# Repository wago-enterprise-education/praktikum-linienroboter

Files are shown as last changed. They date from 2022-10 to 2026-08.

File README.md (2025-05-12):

# Praktikum "Linien Roboter"

Dauer: ~2 Wochen  
Bachelor Projekt von Lisa Lueder  
Anpassungen durch Christian Dück und Finn Erik Hilgers  

## Inhalt

Das Repository beinhaltet das Praktikum "Linienroboter", das für Praktikanten jeden Wissensstandes für ca. 2 Wochen ausgelegt ist.

Die Ordnerstruktur wurde geändert, um die Ressourcen und die Praktikumsaufgaben logisch zu sortieren und das Praktikum übersichtlicher zu unterteilen.
Durch die neue Aufteilung ist es besser möglich, das Praktikum auch für eventuell unterschiedliche Zeiträume aufzuteilen.

### Einführung
- Kennenlernen des ESPs
- Erste Programmierübungen
- Arbeit mit den Sensoren
- Pinout und CheatSheet für den ESP und die Arduino IDE

### Löten
- Lötanleitung
- Aufgaben zum Löten des Linienroboters

### Programmieraufgaben
- Linienverfolgung
- Lichtverfolgung
- Hindernisserkennung
- Überholmanöver
- Webanwendung (Anleitung und allgemeine Idee wurde nie beendet, müsste ausgearbeitet werden)

### Ressourcen - Dateien für die Entwicklung bzw. weiterführende Aufgabenentwicklung
- 3D-Dateien für Felgen und Karosserie
- Platinenpläne
- Grundlegende Praktikums-Ideen
- Materialliste

## Ansprechpartner
- [André Bell](mailto:Andre.Bell@wago.com)
- [Tobias Lauxtermann](mailto:Tobias.Lauxtermann@wago.com)
- [Maik Rehburg](mailto:Maik.Rehburg@wago.com)

## Mitwirkende
- Lisa Rüter
- Christian Dück
- Finn Erik Hilgers
- Michael Kolle
- Louis Krumme
- Kieran Smith

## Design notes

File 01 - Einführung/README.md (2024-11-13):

# Praktikum "Linien Roboter" - Einführung

Version: V1.1  
Dauer: ~2 Wochen  
Bachelor Projekt von Lisa Lueder  
Anpassungen durch Christian Dück und Finn Erik Hilgers  

## Content

Bekanntmachen mit:
- Arduino IDE
- Elektrotechnische Grundlagen
- Informatische Grundlagen

01 -> Einführung in ESP
    Elektrotechnik + Programmiereinführung
        
Programmiereinführung anhand der elektrischen Bauteile, die auch später auf dem Roboter benutzt werden, also Beispiele an der LED, Potentiometer (Als Alternative zu den Photowiderständen) etc.

    Enthalten sind:
    - digitalWrite, digitalRead -> Hinweis zu Liniensensoren
    - pinMode
    - define
    - delay
    - Boolean -> erklärung von High und Low
    - Variablen
    - If-Bedingung
    - analogWrite, analogRead -> Hinweis zu Motoren
    - map

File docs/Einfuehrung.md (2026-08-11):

---
layout: page
title: Linienroboter - Einführung
lang: de
lang-ref: index
---

## Einführung

In der Einführung sollst du dich zunächst mit der Arduino IDE und dem ESP 32 vertraut machen sowie elektro- und informationstechnische Grundlagen erlernen, um später den Linienroboter problemlos aufbauen zu können.
Zuerst solltest du mithilfe der [Materialliste](Material.pdf) alle nötigen Bauteile zusammensuchen. Die Bauteile für diese Einleitung sind nicht in dem Bauteilsatz für den Linienroboter enthalten. Bei der Durchführung der Einführung können dir [dieses Diagramm von den Pins des ESP32](00-Pinout-ESP32-DEVKIT-V1.pdf) und [dieser Arduino Cheat Sheet](00-CheatSheet-Arduino.pdf) helfen.

{: .info}
Diese und die kommenden Anleitungen sollen dich bei deinem Praktikum unterstützen. Falls es zwischendurch Fragen geben sollte oder du anhand der Anleitung nicht weiterkommst, kannst du uns jederzeit [ansprechen](./index.md/#ansprechpartner)!

### Grundsätzliches
Wir beginnen mit dem Mikrocontroller, der den Roboter am Ende steuern wird. Das ist ein ESP32-Entwicklungsboard.

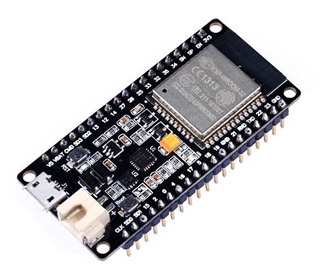
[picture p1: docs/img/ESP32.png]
Abbildung eines ESP32 DEV Board


Der eigentliche Mikrocontroller ist das silberne Quadrat in der oberen Hälfte. Der Rest sind bspw. eine WLAN-Antenne und die Stromversorgung des Mikrocontroller. Solche Mikrocontroller können z.B. für die Auswertung von Sensordaten, die Datenaufnahme oder kleinere Berechnungen eingesetzt werden.
Die Metallstifte an der Seite sind die Anschlüsse für verschiedene Schnittstellen, die der Mikrocontroller unterstützt. Wir nennen sie „Pins“. Welcher Metallstift welche Schnittstelle [unterstützt](00-Pinout-ESP32-DEVKIT-V1.pdf) unterscheidet sich, je nachdem welches Entwicklungsboard man verwendet. Wenn du also selbst zu Hause mit einem ESP32-Board arbeiten möchtest, musst du immer die passende Pin-Belegung („Pinout“) suchen.
Im Praktikum wird vorgegeben, welcher Pin verwendet werden soll.
Der ESP32 kann über verschiedene sogenannte Bus-Schnittstellen kommunizieren, die für uns aber nicht relevant sind. Wir nutzen vor allem die **GPIOs**. Das steht für **G**eneral **P**urpose **I**nput **O**utput, also allgemeine Eingabe und Ausgabe.
Eingaben sind z.B. Werte, die Sensoren aufnehmen und die wir im Programm verarbeiten, Ausgaben sind Signale, um bspw. die Motoren ein- und auszuschalten.

### Aufgabe 1
Wir starten mit einem sogenannten „Hello World“ Programm.
Das ist immer ein möglichst einfaches Programm ohne große Funktionalität, mit dem erst einmal nur getestet wird, ob die Verbindung zu dem Gerät bzw. das Gerät selbst funktioniert. Dafür muss die installierte Arduino IDE gestartet werden. Dann öffnet sich ein leeres Projekt, dass aus zwei Funktionen besteht. Diese beiden Funktionen sind immer der Grund-Bestandteil aller Projeke:
+	_setup()_: Diese Funktion wird beim Starten des ESP32 einmalig ausgeführt und wird genutzt, um die Ein- und Ausgänge den Anschluss-Pins des ESP32 zuzuordnen oder eine Verbindung zu initialisieren.

+	_loop()_: Diese Funktion wird solange das Board eingeschaltet ist wiederholt und zum Abfragen bzw. Beschalten der Ein- und Ausgänge genutzt.
Schreiben Sie zunächst diesen Programm-Code in die Funktionen:

```C
void setup() {
   Serial.begin(9600);
}
  
void loop() {
   Serial.println("Hello World");
   delay(2000);
}
```
#### Verbindung zum ESP32 herstellen
Verbinde den ESP32 mit einem microUSB-Kabel mit einem PC. Das passende ESP32-Board (ESP32 DOIT DEVKIT V1) ist in dieser Version der Arduino IDE schon vor-ausgewählt. Stelle als nächstes den Verbindungsport ein. Unter „Werkzeuge > Ports“ werden die möglichen Ports angezeigt. Jetzt kann das Programm in der Arduino IDE kompiliert und auf den ESP32 geladen werden. Dafür muss das Pfeil-Symbol oben links betätigt werden.
Wenn das Hochladen abgeschlossen ist, lässt sich über _Werkzeuge > Serieller Monitor_ ein weiteres Fenster öffnen, in dem alle 2 Sekunden der Text „Hello World“ ausgegeben wird. Die Kommunikation zwischen dem ESP32 und dem PC funktioniert also.
Dieses neu-geöffnete Fenster ist der Serielle Monitor. Über die Code-Zeile `Serial.begin(9600)` wird eine Verbindung dazu aufgebaut und mit `Serial.println("Hello World")` können dann Text-Zeilen ausgegeben werden. Das kann später, z.B. für Kontroll-Ausgaben, verwendet werden. Falls die Ausgaben nicht menschenlesbar sind, sollte sichergestellt werden, dass die **Baudraten** von Code und seriellem Monitor übereinstimmen.

### Aufgabe 2
#### Das Steckbrett
Die Folgenden Aufgaben werden alle auf einem sogenannten **Steckbrett** oder englisch Breadboard durchgeführt.
Um dieses richtig verwenden zu können, ist es wichtig, zu wissen, wie dieses verbunden ist. Die folgende Grafik stellt innenliegende Brücken anhand orangefarbener Linien dar. Um die folgenden Übungen durchführen zu können, sollte der ESP32 wie abgebildet auf das Board gesteckt werden.

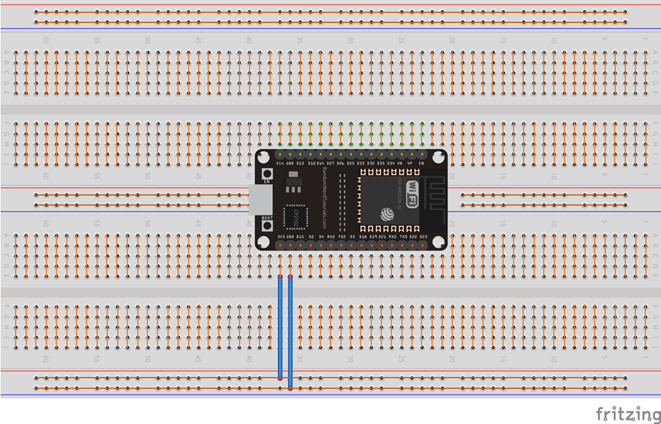
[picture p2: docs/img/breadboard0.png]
Grundanordnung Breadboard


#### LEDs
In dieser Aufgabe soll die **LED** (_Light emitting diod_) oder Leuchtdiode eingeführt werden. 
Wenn durch eine LED Strom fließt, leuchtet sie. Ist der Strom durch die LED zu groß, brennt sie durch. Um das zu verhindern muss immer ein sogenannter Vorwiderstand zwischen der Stromquelle und der LED („vor der LED“) eingebaut werden. Für die folgenden Aufgaben soll immer ein Widerstand von 220 &#8486; verwendet werden.
Wenn du dir die LED genau ansiehst, fällt dir auf, dass sie nicht symmetrisch aufgebaut ist, sondern einer der Anschlussdrähte länger ist. Der lange Anschlussdraht ist der Plus-Pol der LED, der kurze der Minus-Pol. An dieser Seite ist auch das Gehäuse der LED abgeflacht, auch daran lassen sich die Seiten unterscheiden.
Der Strom soll mit dem langen Bein, also dem Plus-Pol verbunden sein.
Baue nun die Schaltung entsprechend des folgenden Bildes auf:

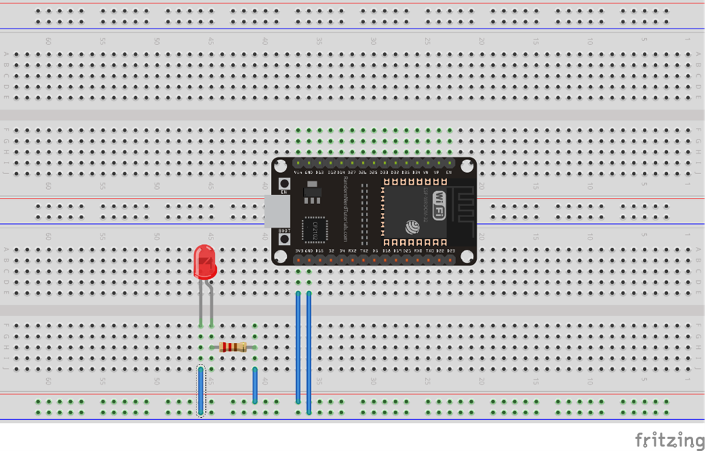
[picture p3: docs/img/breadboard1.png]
LED und Widerstand an den ESP angeschlossen


Leuchtet die LED? - Was passiert, wenn man sie umdreht?

### Aufgabe 3
Mit dem Aufbau der vorherigen Aufgabe liegt immer Spannung an der LED an und sie leuchtet immer.
Wir wollen sie aber selbst über den Mikrocontroller ein- und ausschalten können. Dafür nutzen wir einen Ausgangspin des ESP32, den wir programmieren können. Baue dafür als erstes diese Schaltung auf und öffne ein neues Projekt in der Arduino IDE:

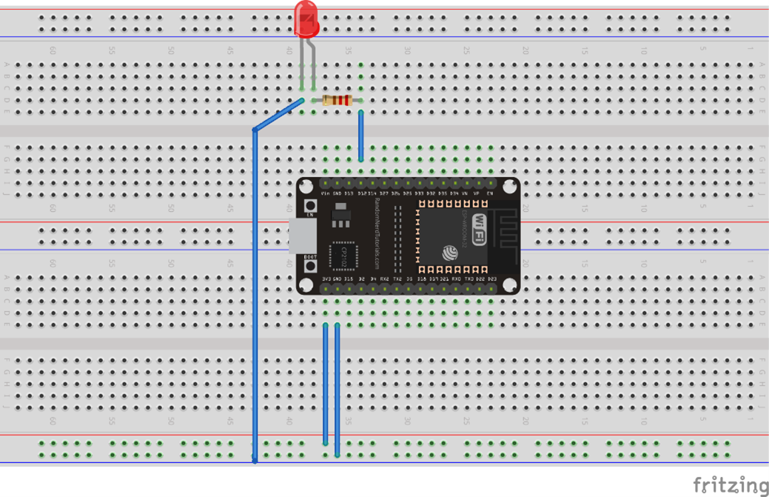
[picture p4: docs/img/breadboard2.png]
LED angeschlossen an Ausgang des Mikrocontrollers


Der Ausgang, an dem der Widerstand angeschlossen ist, ist mit „D12“ bezeichnet. Das ist der Pin mit der Nummer 12. Damit wir nicht im Programm die Nummer verwenden müssen, um die LED ansteuern zu können, „merken“ wir uns den Pin und definieren dafür eine eigene Bezeichnung. Das macht man durch `#define <Platzhalter> <Wert>`, dass man über die Loop- und Setup-Funktion schreibt. In diesem Fall also:

```C
#define LED 12
```
Jetzt müssen wir noch konfigurieren, dass dieser Pin als Ausgang genutzt werden soll. Das muss nur einmal beim Starten des ESP ausgeführt werden und wird daher in die _Setup()_-Funktion geschrieben. Die Funktion, um einen digitalen Ein- oder Ausgang zu konfigurieren ist `pinMode(<Pin>, <INPUT/OUTPUT>)`.
Für alle Stellen im Programm, in denen die Pin Nummer benötigt wird, können wir jetzt den Platzhalter eintragen, also:
```C
pinMode(LED, OUTPUT);
```
Damit „weiß“ das Programm, dass dieser Pin, an den die LED über den Vorwiderstand angeschlossen ist, einen Wert High/Low ausgeben soll. Im nächsten Schritt müssen wir das auf diesen Pin schreiben. Das soll immer wieder passieren, muss also in die loop()-Funktion geschrieben werden.
Ein digitaler Wert hat immer zwei Zustände: 0 und 1 bzw. true/false, HIGH/LOW.
Um einen Ausgang ein- oder auszuschalten, muss die Funktion `digitalWrite(LED, HIGH);` aufgerufen werden.
Mit HIGH wird die LED eingeschaltet. Um sie wieder auszuschalten, schreibt man LOW statt HIGH. Eine blinkende LED schaltet sich in festgelegten Abständen immer wieder an und aus. Um diesen Abstand zu programmieren, nutzt man `delay(<Zeit in Millisekunden>);`
Schreibe nun ein Programm, welches anhand der nun bekannte Funktionen die LED alle 2 Sekunden blinken lässt.

### Aufgabe 4
Bisher haben wir einen Pin als Ausgang definiert und benutzt. Ebenso wichtig ist es, Eingänge lesen zu können.
Ergänze daher deinen Aufbau um die folgenden Komponenten:

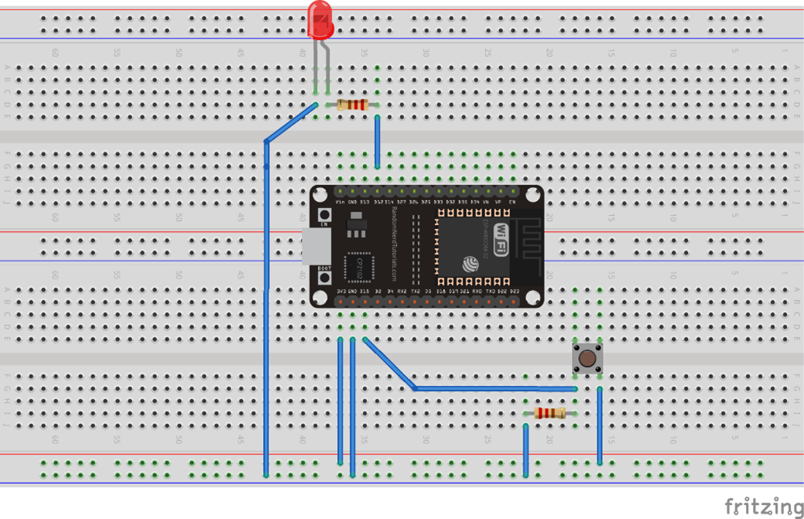
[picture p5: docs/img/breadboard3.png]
ESP32 mit digitalem Eingang (Taster) und digitalem Ausgang (LED)


Die LED ist weiterhin an Pin 12 angeschlossen. Die Konfiguration können wir daher beibehalten. Zusätzlich ist jetzt ein Taster an Pin 15 hinzugekommen. Definieren Sie auch dafür wieder einen Platzhalter und konfigurieren Sie den Pin als Eingang. 
Die LED ist weiterhin an Pin 12 angeschlossen. Die Konfiguration können wir daher beibehalten. Zusätzlich ist jetzt ein Taster an Pin 15 hinzugekommen. Definiere auch dafür wieder einen Platzhalter und konfiguriere ihn als Eingang. Nutze dafür die Syntax, die du aus den vorherigen Aufgaben kennst.
Jetzt wollen wir lesen, ob der Taster betätigt wird oder nicht. Da dies durchgehend geprüft werden soll, wird auch dies in der loop()-Funktion programmiert. Wir nutzen die Funktion: 

```C
digitalRead(<Pin>);
```
Dafür geben wir an, welchen Pin wir auslesen wollen. Die Funktion gibt dann entweder HIGH oder LOW zurück. Diesen Wert speichern wir um ihn anschließend weiterzuverwenden. Dafür legen wir eine Variable an. Variablen sind die Speicher eines Programms und haben immer einen Typ, einen Namen und einen Wert. Der Typ legt fest, was in der Variable gespeichert werden kann. Das Anlegen funktioniert nach dem folgenden Schema:

```
<Typ> <Name> = <Wert>;
```
Die Variable, die wir anlegen, muss vom gleichen Typ wie der Rückgabewert der Funktion sein. Zahlenwerte sind meist sogenannte Integer `int`, digitale Werte sind boolsche Variablen `bool`.
Da wir einen digitalen Wert einlesen, erhalten wir entweder HIGH oder LOW bzw. true oder false.
Wir können die Variable so deklarieren:

```C
bool tasterWert;
tasterWert = digitalRead(<PIN>);
```
Um den Zustand einer Variablen zu überprüfen, kann man _if-Bedingungen_ verwenden.
Beispiel: Wenn es kalt ist, mache die Heizung an:

```C
if (Raum == kalt){
    Heizung = an;
}
```
If-Statements können beliebig ergänzt werden:

```C
if (Bedingung){
    Anweisung 1;
} elsif {
    Anweisung 2;
} else{
    Anweisung 3;
}
```
Versuche nun die LED dann anzuschalten, wenn der Taster gedrückt ist.

### Aufgabe 5
#### Funktionsweise eines Potentiometer
Für die Programmierung des Roboters brauchen wir später nicht nur digitale Ein- und Ausgänge, sondern auch analoge.
Diese können nicht nur HIGH oder LOW sein, sondern mehrere verschiedene (Zahlen-)Werte annehmen.
Um zunächst verschiedene Werte an einem Eingang zu lesen, nutzen wir ein Potentiometer. Das ist ein mechanisch einstellbarer Widerstand.
Der Widerstandswert, zwischen den beiden äußeren Anschlüssen, ist fest. Am mittleren, dritten Anschluss ist der bewegliche Kontakt, dessen Widerstand man durch Drehen verstellen kann. Wenn man an die äußeren Anschlüsse eine Spannung anlegt, erhält man einen einstellbaren Spannungsteiler. Was das bedeutet, können wir mit einem Multimeter anschauen. Baue dafür die abgebildete Schaltung auf. Miss dann mit einem Multimeter zuerst die Spannung zwischen den äußeren Anschlüssen des Potentiometers und dann die zwischen dem mittleren Anschluss und dem Ground-Anschluss. 
Was passiert, wenn man am Potentiometer dreht? 

#### Einlesen analoger Eingänge

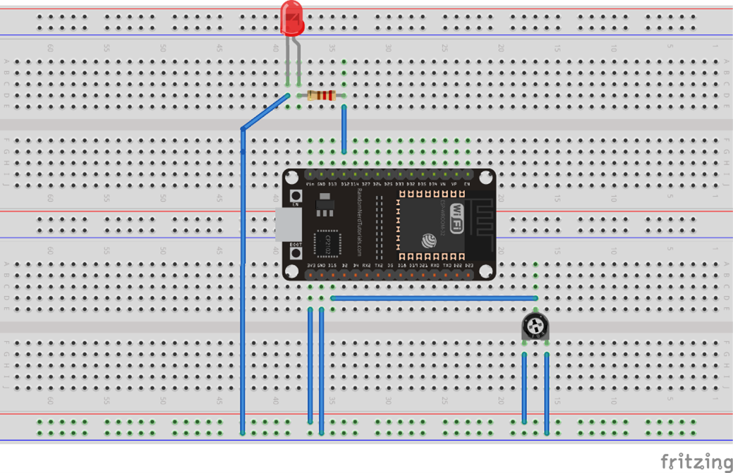
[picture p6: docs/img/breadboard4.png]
Taster durch Potenziometer ersetzt


Die Gesamtspannung an den äußeren Anschlüssen teilt sich entsprechend des Widerstandsverhältnisses auf. Wenn man durch Drehen den Widerstand verändert, verändert sich auch die Spannung, die über dem Teil-Widerstand abfällt. Das können wir auch am Anschluss des ESP32 messen und für unser Programm nutzen.
Die Funktion, die wir dafür nutzen lautet `analogRead(<Pin>);`
Diese liest den analogen Eingang aus. Wie bei der vorherigen Aufgabe kann man den Wert auch in einer Variablen speichern. Dieser Rückgabewert ist vom Typ `int`. Die Funktion `analogRead()` kann Werte zwischen 0 und 4095 einlesen.

#### Schreiben analoger Ausgänge
Jetzt wollen wir durch das Drehen des Potentiometers eine LED dimmen. Dafür nutzen wir die Funktion:

```C
analogWrite(<Pin>, <Wert>);
```
Mit `analogWrite()` kann man 256 verschiedene Helligkeiten einer LED einstellen, angefangen mit 0 für aus und 255 für volle Stärke.
Unpraktischerweise kann man 4096 verschiedene Werte einlesen, aber nur 256 Werte ausgeben. Um diese miteinander zu verbinden, verwendet man den Befehl `map()`.
Der Befehl wird so verwendet:

```C
map(analogRead(<Pin>),0,4096,0,255);
```
Versuche, den Befehl selbst nachzuvollziehen oder nimm das [Cheat Sheet](00-CheatSheet-Arduino.pdf) zur Hilfe.

### Aufgabe 6
Genauso, wie du in der vorherigen Aufgabe die LED über einen analogen Wert angesteuert hast, kann man zum Beispiel auch einen „Beeper“, das ist ein kleiner Lautsprecher, ansteuern.

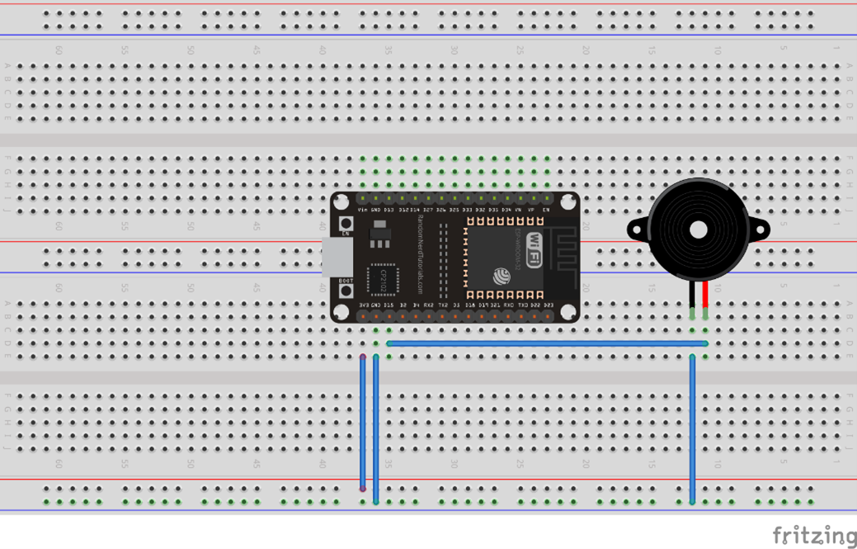
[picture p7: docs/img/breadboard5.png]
ESP mit Beeper


Um den Ton des Beepers verändern zu können, muss man sich der Funktion `ledcWrite(<Pin>,<Wert>)` bedienen.
Mit dieser ist es möglich im Gegensatz zu `analogWrite()` nicht die Abstände zwischen zwei Stromimpulsen, sondern die Frequenz des Signals zu ändern, wodurch sich der Ton ändert.
Um `ledcWrite()` verwenden zu können, müssen wir den Pin zusätzlich zum `pinMode()` mit `ledcAttach(<Pin>,<Frequenz>,8)` im Setup initialisieren.
Der Ton verändert sich mit der eingestellten Frequenz. Probiere verschiedene Frequenzen aus – welcher Ton ist am angenehmsten? Merke dir den zugehörigen Wert, den Beeper brauchen wir später als Hupe für den Roboter!

| | |
|:--- | ---:  |
|<a href="./index.html"><- Startseite</a>|<a href="./Aufbauanleitung.html">Aufbauanleitung -></a>|

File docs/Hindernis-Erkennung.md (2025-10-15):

---
layout: page
title: Linienroboter - Hindernis erkennen
lang: de
lang-ref: index
---

## Hindernis erkennen
Damit der Roboter Hindernisse erkennt, nutzen wir einen Ultraschall-Sensor. 

Die Messung wird gestartet durch:
```C
    digitalWrite(<ABSTAND_TRIGGER>, HIGH);
    delayMicroseconds(10);
    digitalWrite(<ABSTAND_TRIGGER>, LOW);
    Time = pulseIn(DISTANCEECHO, HIGH); // Receive Signal
    Distance = (Time/2)*0.03432; // Distance in cm
```

{:.info}
Der Pin `ABSTAND_TRIGGER` gibt einen Ultrschallton aus, ist also ein _OUTPUT_. Das Mikrofon `DISTANCEECHO`, zeichnet die Länge auf, die der Schall nachläuft, wenn der Ton nicht mehr generiert wird. Es mus daher als _INPUT_ initialisiert werden. 

Füge anschließend den Hindernis-Sensor zum Programm hinzu. Der Roboter soll in keinem Fahrmodus (Licht oder Linie Folgen) mit einem Hindernis kollidieren.

So sieht das Signal des Ultraschallsensors aus:

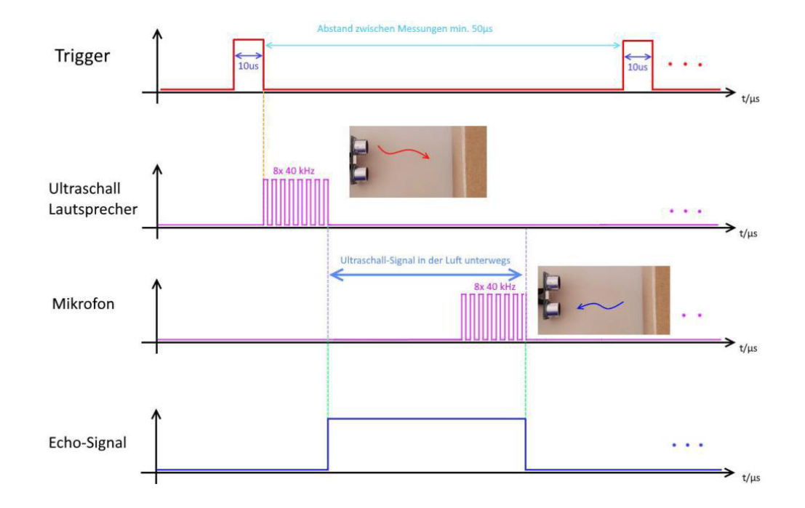
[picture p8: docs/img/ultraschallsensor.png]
Funktion des Ultraschallsensors


| | |
|:--- | ---:  |
|<a href="./Licht-Folgen.html"><- Licht folgen</a>|<a href="./Hindernis-ueberholen.html">Hindernis überholen -></a>|

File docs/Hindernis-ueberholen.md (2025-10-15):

---
layout: page
title: Linienroboter - Hindernis überholen
lang: de
lang-ref: index
---

## Hindernis überholen

Jetzt nutzen wir die Linien- und Hindernissensoren in Kombination, um ein Hindernis zu Überholen. Baue dafür als erstes mit drei Linien auf dem Boden eine zweispurige Straße auf.

Der Roboter fährt zunächst zwischen zwei Linien auf der rechten Spur. Wenn ein Hindernis auf der eigenen Spur erkannt wird, soll der Roboter in ausreichendem Abstand halten. Dafür muss der Roboter die Mittellinie der Straße überfahren und dann auf der linken Fahrspur zurückfrahren.

Wenn während des Überholvorganges ein Hindernis auf der linken Spur erkannt wird, soll der Roboter hupen und anhalten. Wird das Hindernis entfernt, kann der Roboter weiterfahren und den Überholvorgang fortsetzen.

Auf der nächsten Seite sind die Schritte noch einmal grafisch erklärt.

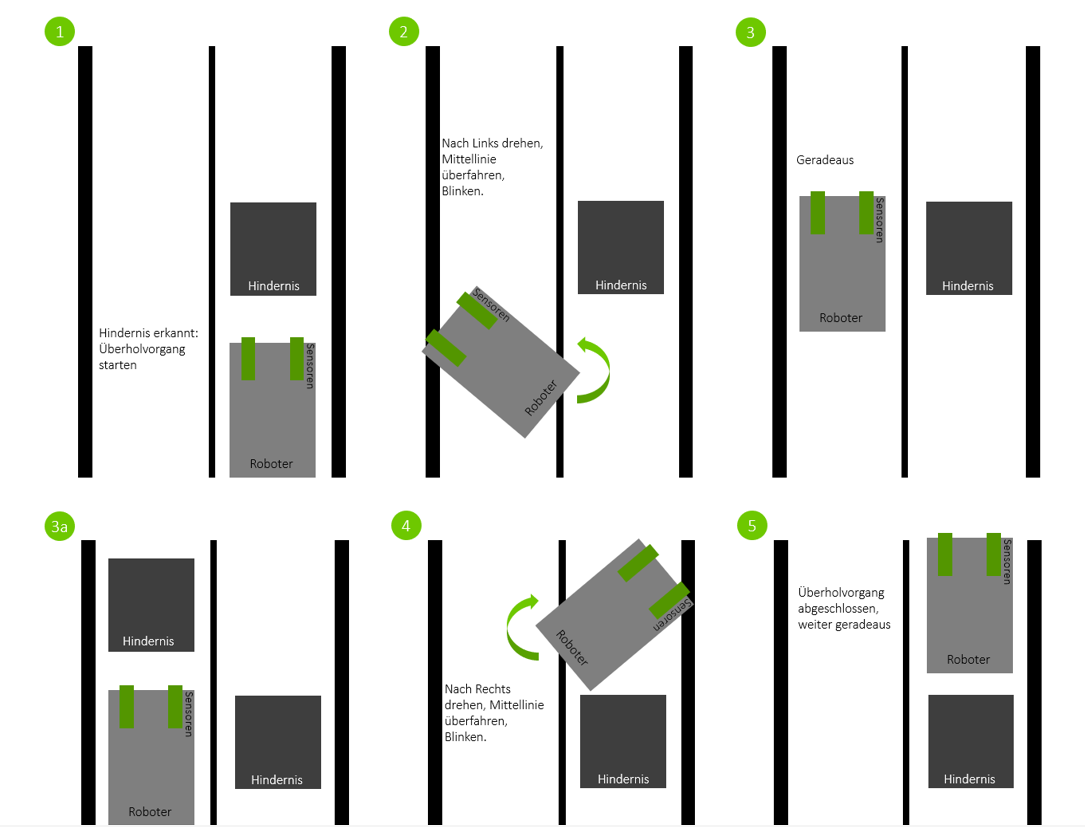
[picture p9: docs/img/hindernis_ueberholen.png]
Ueberholen1


| | |
|:---|---:|
|<a href="./Hindernis-Erkennung.html"><- Hindernis erkennen</a>|<a href="./Webserver.html">Webserver -></a>|

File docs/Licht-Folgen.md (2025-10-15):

---
layout: page
title: Linienroboter - Licht folgen
lang: de
lang-ref: index
---

## Licht folgen

Als nächstes soll der Roboter dem Licht einer Taschenlampe folgen können. Dafür nutzen wir die Fotowiderstände. Man nennt diese Bauteile auch LDR ("Light Dependent Resistor"). Das sind Widerstände, deren Widerstandswerte lichtabhängig sind. Je mehr Licht auf einen Fotowiderstand fällt, umso kleiner ist der Widerstandswert.

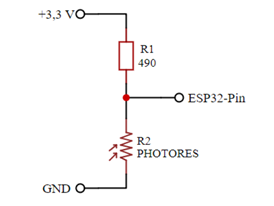
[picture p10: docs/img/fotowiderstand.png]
Fotowiderstand


Auf der Platine ist der Fotowiderstand in einem Spannungsteiler mit einem 470 Ω Widerstand. Die Gesamtspannung, die über den beiden Widerständen abfällt, ist immer gleich. Ändert sich der Wert des Widerstandes, ändert sich auch die Teilspannung _U_, die darüber abfällt. Diese Spannung liegt am Eingang des ESP32 an. Die Veränderung können wir also wieder, wie bei dem Potentiometer aus den Aufgaben in Teil 1, über einen analogen Eingang auswerten.

Lass dir die Werte der Sensoren zunächst im Seriellen Monitor ausgeben und schaue, wie sich die Werte entwickeln, wenn sich die Helligkeit verändert. Da das Tageslicht durch ein Fenster viel stärker ist als das einer Taschenlampe, müssen z. B. auch verschiedene Tageszeiten oder die Helligkeit in Räumen beachtet werden.

Der ausgelesene Wert lässt sich mithilfe eines zuvor gelernten Befehls in Motorstärke „umformen“. Da für den Befehl die übergebenen Werte nur innerhalb eines bestimmten Bereichs sein dürfen, verwenden wir den Befehl
`constrain(x, minWert, maxWert);`

| | |
|:--- | ---:  |
|<a href="./Linie-folgen.html"><- Linie folgen</a>|<a href="./Hindernis-Erkennung.html">Hindernis erkennen -></a>|

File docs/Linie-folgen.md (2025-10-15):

---
layout: page
title: Linienroboter - Linie-Folgen
lang: de
lang-ref: index
---

## Linie folgen

<span style="color: red; font-weight: bold; text-decoration: underline;">Achtung:</span>
Die Steckbrücke auf dem 2-poligen Stecker, also der Jumper muss <span style="text-decoration: underline;">immer</span> abgezogen werden, wenn der ESP32 über ein USB-Kabel mit deinem PC verbunden ist! Sind die Batterie und der ESP32 gleichzeitig an die Bauteile angeschlossen, kann das zu Problemen führen!

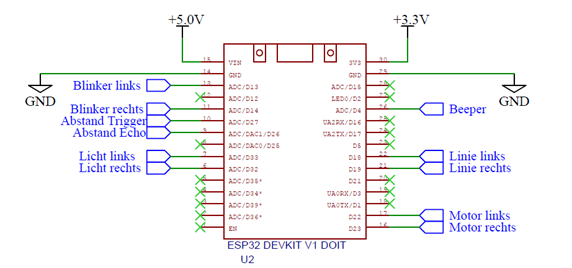
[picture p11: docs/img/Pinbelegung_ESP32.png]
Abbildung der Pinnbelegung


Obenstehend siehst du eine Abbildung der Pins des ESP32. In <span style="color: blau;">blau</span> eingezeichnet sind die einzelnen Bauteile des Roboters, verbunden mit dem jeweiligen Pins. Im Programm musst du die Pins auch entsprechend mit dem Bauteilen verknüpfen, also die Pins entsprechend definieren mit dem Befehl:
```C

#define <Bezeichnung> <PinNummer>

```
Dies ist Platinen bedingt und kann nicht geändert werden. Die Pin-Nummer ist hierbei die Zahl die <span style="text-decoration: underline;">in dem Kasten</span> steht. also bei "Blinker links - D13" ist die Pin-Nummer 13. Die Zahl außerhalb von dem Kasten ist hier nicht zu beachten.

Theoretisch ließe sich das Programm auch nur durch Pin-Nummern umsetzen, allerdings ist es mit den alternativen-Bezeichnungen viel übersichtlicher.

### Aufgabe 1: "Linie Folgen"
Kombiniere die vorherigen Aufgaben so, dass dein Roboter einer Linie folgen kann.

Als Linie funktioniert ein dünnes, schwarzes Klebeband oder Isolierband, dass auf einem weißen Tisch im Kreis gezogen wurde.

### Aufgabe 2: "Blinken"
Nutze die LEDs auf der Platine als Blinker des Roboters. Es soll die linke LED blinken, wenn der Roboter eine Linkskurve fährt und umgekehrt.

### Aufgabe 3: "Hupen"
Nutze den Beeper als Hupe des Roboters. Wenn beide Liniensensoren die Farbe der Linie erkennen, soll die Hupe "betätigt werden"

| | |
|:--- | ---:  |
|<a href="./Aufbauanleitung.html"><- Aufbauanleitung</a>|<a href="./Licht-Folgen.html">Licht folgen -></a>|

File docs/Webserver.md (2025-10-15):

---
layout: page
title: Linienroboter - Webserver
lang: de
lang-ref: index
---
## Webserver
Um den Linienroboter fernsteuern zu können, steht der Code für einen Webserver zur Verfügung. Über diesen Webserver kann man den Roboter bequem über eine Website steuern.

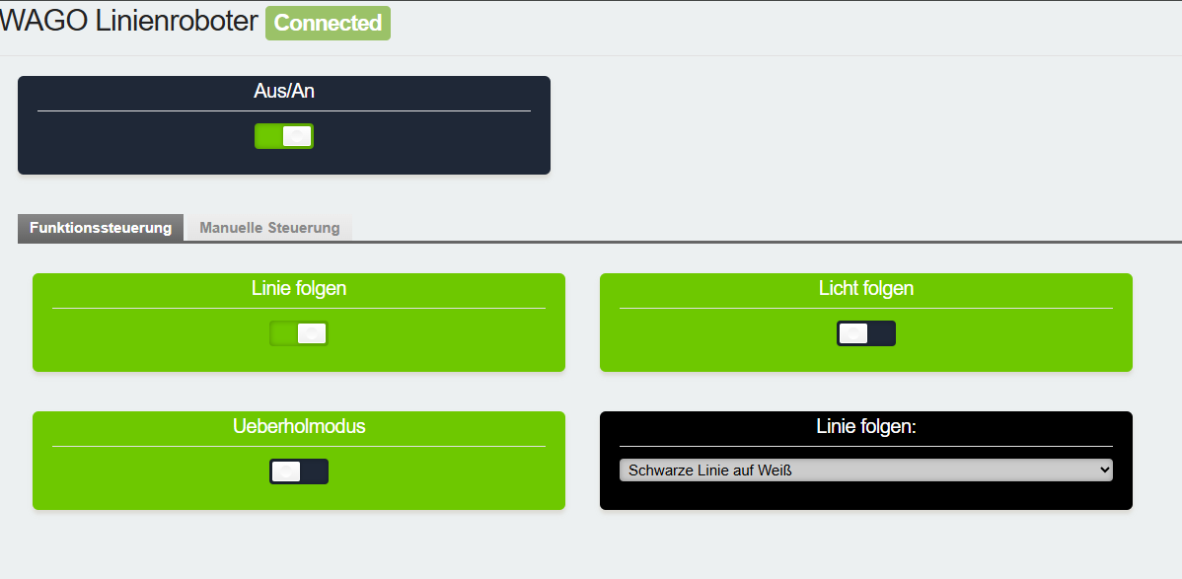
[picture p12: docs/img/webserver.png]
Bildschirmfoto der Webanwendung


### Vorbereitung
Um den Webserver nutzen zu können, müssen der Arduino IDE einige Bibliotheken hinzugefügt werden:
+ "ESP Async WebServer" von "ESP32Async"
+ "Async TCP" von "ESP32Async"
+ "ESPUI" von "Lukas Bachschwell"

{:.info}
Bibliotheken können über den Bibliotheksverwalter in der linken Seitenleiste installiert werden.

Des Weiteren muss der [Code für den Webserver](Webserver.cpp) in das Quellverzeichnis des Arduinosketches gespeichert werden. In der `.ino`-Datei muss dieser dann aufgerufen werden:

```C
#include Webserver.cpp
```

In der `setup()`-Funktion muss der Server initialisiert und die `start()`-Methode aufgerufen werden:

```C
Webserver server;
server.start("ESP32", "");
```
Dabei ist der erste Teil vor dem Komma der Name des Netzwerks und der Teil dahinter das Passwort, welches leer bleiben kann.
In der `loop()`-Funktion muss `server.getPadBack();` aufgerufen werden.

Beispiel:

```C
#include "Webserver.cpp"

Webserver server;

void setup(){
    Serial.begin(9600);
    server.start("ESP32", "");
}

void loop(){
    server.getPadBack();
}
```
### Webserver öffnen
Um den Webserver nutzen zu können, musst du dein Handy oder deinen PC entsprechend der Angaben aus dem Code mit dem Netzwerk des ESP32 verbinden.
Der Webserver ist unter der IP-Adresse des ESP32 `192.168.4.1` zu erreichen. Sollte die Adresse abweichen, kann sie auch im seriellen Monitor abgelesen werden.

### Codeanpassungen
Jetzt muss nur noch der Code angepasst werden, um die Funktionen des Webservers zu nutzen.
Die Funktionen, welche du bereits programmiert hast, sollen nur aktiv werden, wenn der jeweilige Button auf der Weboberfläche gedrückt ist. Hierfür müssen die Codeblöcke in ein _if_-Statement eingebettet werden.

```C
if(server.getObstacleButton()){
	//Dein Code, welcher ausgeführt werden soll
}
```
Welche Funktionen es gibt, kann man über die Autocompletion der IDE (_Str+Leertaste_) oder die Datei Webserver.cpp einsehen.

| | |
|:---|---:|
|<a href="Hindernis-ueberholen.html"><- Hindernis überholen</a>||

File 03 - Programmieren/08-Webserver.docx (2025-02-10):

# Praktikum Linienroboter

Aufgabe Webserver:

Um die Websteuerung des Linienroboters zu aktivieren, muss die Datei Webserver.cpp heruntergeladen werden. Dabei müssen sich die Datei Webserver.cpp und ihr Code im selben Ordner befinden. Weiterhin müssen im Code des Programms ein paar Änderungen vorgenommen und einige Bibliotheken installiert werden. Es werden die Bibliotheken „ESP Async WebServer“ von „ESP32Async“ (Version 3.7.0), „Async TCP“ von „ESP32Async“ und „ESPUI“ von „Lukas Bachschwell“ (Version 2.2.4.) benötigt.

Öffnen Sie das entsprechende Untermenü, indem sie auf das Symbol der Bücher klicken, um die Bibliotheken zu installieren.

In der Suchleiste geben sie dann die Namen der Bibliotheken ein und klicken auf „INSTALL“

Zudem muss die Datei Webserver.cpp im Code eingebunden werden. Hierfür muss der Befehl

#include "Webserver.cpp" benutzt und in der ersten Zeile im Code stehen.

Danach muss eine Instanz von Webserver über das Setup erstellt werden:

Webserver server:

Weiterhin wird im Setup die Methode start() von dem Objekt server aufgerufen werden:

server.start("ESP32", "");

Dabei ist der erste Teil vor dem Komma der Name des Netzwerks und der Teil dahinter das Passwort, welches leer bleiben kann.

Im Loop wird dann die Funktion server.getPadBack(); aufgerufen.

Als Beispiel:

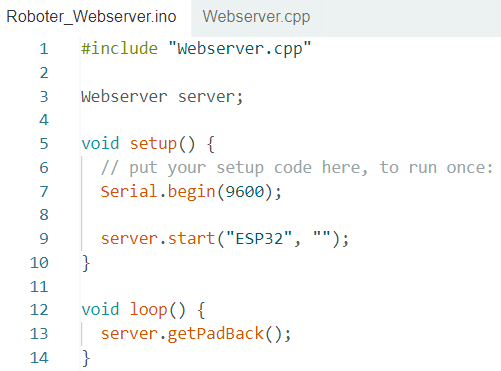
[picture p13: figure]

# Praktikum Linienroboter

Danach ist es möglich ein Handy mit dem Netzwerk des Controllers zu verbinden, welches den Namen aus server.start(); bekommt.

Als nächstes muss im Browser die IP-Adresse des Controllers eingeben, um auf den Webserver weitergeleitet zu werden. Die IP-Adresse wird auf dem Seriellen monitor ausgegeben oder steht in den Details der Wlan-verbindung entweder unter Router oder Gateway. In der Regel sollte die IP 192.168.4.1 sein.

Codeanpassung

Jetzt muss nur noch Ihr Code angepasst werden, um die Funktionen des Webservers zu nutzen. Die Funktionen, welche bereits geschrieben wurden, sollen nur aktiv werden, wenn der jeweilige Button auf der Weboberfläche gedrückt ist. Hierfür müssen die Codeblöcke in ein If-Statement eingebettet werden.

Beispiel:

If(server.getObstacleButton()){

//Dein Code, welcher ausgeführt werden soll

}

Alle wichtigen Methoden sind in der Datei Webserver.cpp vorhanden.

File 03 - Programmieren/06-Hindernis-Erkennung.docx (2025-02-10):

# Praktikum Linienroboter

Teil 6: „Hindernis Erkennen“

Version 1.2, 10.02.2025

Damit der Roboter Hindernisse erkennt, nutzen wir einen Ultraschall-Sensor.

Die Messung wird gestartet durch:

digitalWrite(<ABSTAND_TRIGGER>, HIGH);

delayMicroseconds(10);

digitalWrite(<ABSTAND_TRIGGER>, LOW);

Time = pulseIn(DISTANCEECHO, HIGH); // Receive Signal

Distance = (Time/2)*0,03432; // Distance in cm

Fügen Sie anschließend den Hindernis-Sensor zu Ihrem Programm hinzu. Der Roboter soll in keinem Fahrmodus (Licht oder Linie Folgen) mit einem Hindernis kollidieren.

So sieht das Signal des Ultraschallsensors.

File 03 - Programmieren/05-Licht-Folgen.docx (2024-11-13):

# Praktikum Linienroboter

Teil 5: „Licht Folgen“

Version 1.2, 06.11.2024

Als nächstes soll der Roboter dem Licht einer Taschenlampe folgen können. Dafür nutzen wir die Fotowiderstände. Man nennt diese Bauteile auch LDR („Light Dependent Resistor“). Das sind Widerstände, deren Widerstandswert lichtabhängig ist. Je mehr Licht auf einen Fotowiderstand fällt, umso kleiner ist der Widerstandswert.

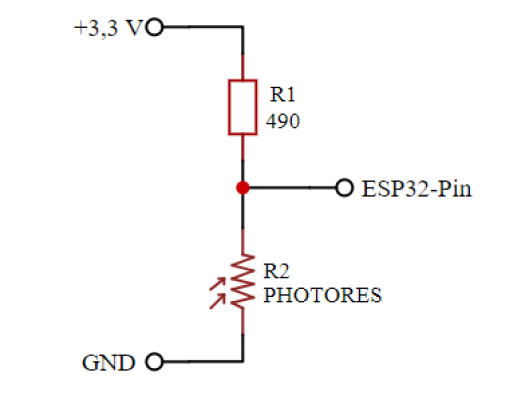
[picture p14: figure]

U

3,3 V

Auf der Platine ist der Fotowiderstand in einem Spannungsteiler mit einem 470 Ω Widerstand. Die Gesamtspannung, die über den beiden Widerständen abfällt, ist immer gleich. Aber wenn sich der Widerstandswert des Fotowiderstands ändert, ändert sich auch die Teil-Spannung U, die darüber abfällt. Diese Spannung liegt am Eingang des ESP32 an. Die Veränderung können wir also wieder, wie bei dem Potentiometer aus den Aufgaben in Teil 1, über einen analogen Eingang auswerten.

Lassen Sie sich die Werte der Sensoren zunächst im Seriellen Monitor ausgeben und schauen Sie, wie sich die Werte verändern, wenn sich die Helligkeit verändert. Das Tageslicht durch ein Fenster ist viel stärker als das einer Taschenlampe, beachten sie also auch z.B. verschiedene Tageszeiten oder abgedunkelte Räume.

Der ausgelesene Wert lässt sich mithilfe eines zuvor gelernten Befehls in Motorstärke „umformen“. Um da für den Befehl der übergebene Wert nur innerhalb eines bestimmten Bereichs sein darf, verwenden wir den Befehl

constrain(x, minWert, maxWert);

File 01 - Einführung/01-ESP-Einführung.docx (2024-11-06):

# Praktikum Linienroboter

Teil 1: Einführungsaufgaben

Version 1.2, 06.11.2024

Das Ziel dieses Praktikums ist es, einen Roboter, der mit Sensoren einer Linie folgen kann aufzubauen und zu programmieren. Damit das gut funktioniert, beginnen wir zunächst mit einigen Einführungsaufgaben, um die Grundlagen der Programmierung und einige Bauteile kennenzulernen.

Diese und die kommenden Anleitungen sollen Sie bei Ihrem Praktikum unterstützen. Falls es zwischendurch Fragen geben sollte oder Sie nur anhand der Anleitung nicht weiterkommen, können Sie uns jederzeit ansprechen!

## Aufgabe 1: "Hello World“-Programm auf Mikrocontroller

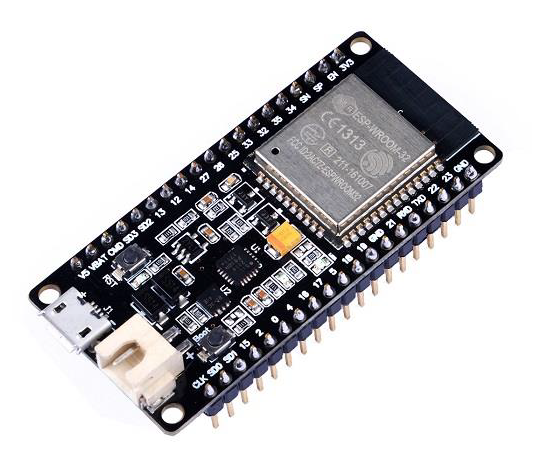
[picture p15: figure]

Wir beginnen mit dem Mikrocontroller, der den Roboter am Ende steuern wird. Das ist ein ESP32-Entwicklungsboard.

Der eigentliche Mikrocontroller ist das silberne Quadrat in der oberen Hälfte. Der Rest sind bspw. eine WLAN-Antenne und die Stromversorgung des Mikrocontroller. Solche Mikrocontroller können z.B. für die Auswertung von Sensordaten, die Datenaufnahme oder kleinere Berechnungen eingesetzt werden.

Die Metallstifte an der Seite sind die Anschlüsse für verschiedene Schnittstellen, die der Mikrocontroller unterstützt. Wir nennen sie „Pins“. Welcher Metallstift welche Schnittstelle unterstützt unterscheidet sich, je nachdem welches Entwicklungsboard man verwendet. Wenn Sie also selbst zu Hause mit einem ESP32-Board arbeiten wollen, suchen Sie immer die passende Pin-Belegung („Pinout“). Im Praktikum wird vorgegeben, welcher Pin verwendet werden soll, sodass Sie sich darüber keine Gedanken machen müssen. Der ESP32 kann über verschiedene sogenannte Bus-Schnittstellen kommunizieren, die für uns aber nicht relevant sind. Wir nutzen vor allem die GPIOs. Das steht für General Purpose Input Output, also allgemeine Eingabe und Ausgabe. Eingaben sind z.B. Werte, die Sensoren aufnehmen und die wir im Programm verarbeiten, Ausgaben sind Signale, um bspw. die Motoren ein- und auszuschalten.

Wir starten mit einem sogenannten „Hello World“ Programm. Das ist immer ein möglichst einfaches Programm ohne große Funktionalität, mit dem erst einmal nur getestet wird, ob die Verbindung zu dem Gerät bzw. das Gerät selbst funktioniert. Dafür starten Sie die Arduino IDE aus dem Ordner „arduino-1.8.13-windows-portable“. Dann öffnet sich ein leeres Projekt, dass aus zwei Funktionen besteht. Diese beiden Funktionen sind immer der Grund-Bestandteil aller Projeke:

- setup(): Diese Funktion wird beim Starten des ESP32 einmalig ausgeführt und wird genutzt, um die Ein- und Ausgänge den Anschluss-Pins des ESP32 zuzuordnen oder eine Verbindung zu initialisieren.
- loop(): Diese Funktion wird solange das Board eingeschaltet ist wiederholt und zum Abfragen bzw. Beschalten der Ein- und Ausgänge genutzt.

Schreiben Sie zunächst diesen Programm-Code in die Funktionen:

void setup() {

Serial.begin(9600);

}

void loop() {

Serial.println("Hello World");

delay(2000);

}

Verbindung zum ESP32 herstellen

Verbinden Sie den ESP32 mit einem microUSB-Kabel mit Ihrem PC. Das passende ESP32-Board ist in dieser Version der Arduino IDE schon vor-ausgewählt. Stellen Sie als nächstes den Verbindungsport ein. Unter „Werkzeuge > Ports“ werden die möglichen Ports angezeigt. Wenn Sie nicht sicher sind, an welchem Port der ESP32 angeschlossen ist, schauen Sie im Geräte-Manager des PCs. Jetzt können Sie in der Arduino IDE das Programm kompilieren und auf den ESP32 laden. Klicken Sie dafür auf das Pfeil-Symbol.

Wenn das Hochladen abgeschlossen ist, klicken Sie auf „Werkzeuge > Serieller Monitor“. Es öffnet sich ein weiteres Fenster, in dem alle 2 Sekunden der Text „Hello World“ ausgegeben wird. Die Kommunikation zwischen dem ESP32 und dem PC funktioniert also.

Dieses neu-geöffnete Fenster ist der Serielle Monitor. Über die Code-Zeile Serial.begin(9600)wird eine Verbindung dazu aufgebaut und mit Serial.println("Hello World") können dann Text-Zeilen ausgegeben werden. Das können Sie auch später, z.B. für Kontroll-Ausgaben, nutzen. Falls die Ausgaben nicht dem Entsprechen, was Sie ausgeben wollen, überprüfen Sie die „baud-Rate“ des Seriellen Monitors. Sie sollte ebenfalls 9600 sein.

Für die kommenden Aufgaben nutzen Sie ein Steckbrett, auf dem Sie verschiedene Schaltungen aufbauen. Auf einem solchen Steckbrett sind die Verbindungspunkte immer entweder in einer Zeile oder Spalte miteinander verbunden, das ist in der folgenden Grafik durch die orangen Linien dargestellt. Stecken Sie den ESP32 wie in der Abbildung dargestellt auf das Steckbrett.

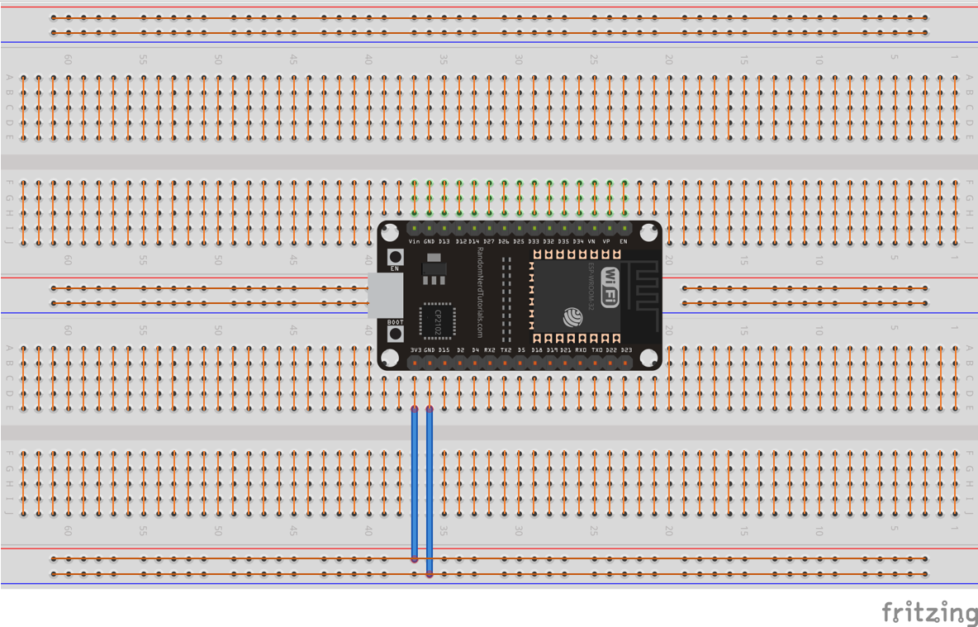
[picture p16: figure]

## Aufgabe 2: Sperr-/ Durchlassrichtung einer LED

In dieser Aufgabe sollen sie Leuchtdioden (LED) kennenlernen. Wenn durch eine LED Strom fließt, leuchtet sie. Ist der Strom durch die LED zu groß, brennt sie durch. Um das zu verhindern muss immer ein sogenannter Vorwiderstand zwischen der Stromquelle und der LED („vor der LED“) eingebaut werden. Für die folgenden Aufgaben nutzen Sie bitte immer einen 220 Ω Vorwiderstand.

Wenn Sie die LED anschauen, fällt Ihnen auf, dass sie nicht symmetrisch aufgebaut ist, sondern einer der Anschlussdrähte länger ist. Der lange Anschlussdraht ist der Plus-Pol der LED, der kurze der Minus-Pol (an dieser Seite ist auch das Gehäuse der LED abgeflacht, auch daran können Sie die Seiten unterscheiden). Der Strom soll mit dem langen Bein, also dem Plus-Pol verbunden sein.

Bauen Sie die Steckbrett-Schaltung der folgenden Abbildung auf. Vom „GND“-Pin des ESP32 gehen Sie mit einer Jumper-Leitung dabei auf die blau markierte Reihe, von dem „3V3“-Pin auf die rot markierte Reihe. Sie können für spätere Schaltungen dann Ground (0V) bzw. 3,3V von diesen Reihen übernehmen.

Leuchtet die LED? Was passiert, wenn Sie sie umdrehen?

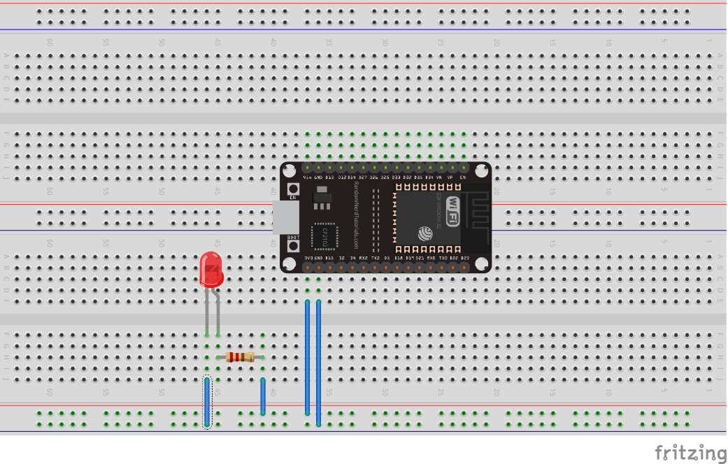
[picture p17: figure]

## Aufgabe 3: LED blinken lassen

Mit dem Aufbau der vorherigen Aufgabe liegt immer Spannung an der LED an und sie leuchtet immer. Wir wollen sie aber selbst ein- und ausschalten können. Dafür nutzen wir einen Ausgangspin des ESP32, den wir programmieren können. Bauen Sie dafür als erstes diese Schaltung auf und öffnen Sie ein neues Projekt in der Arduino IDE:

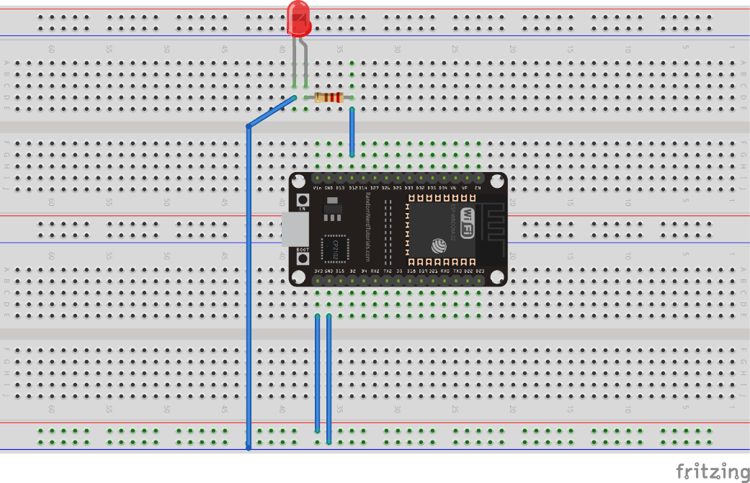
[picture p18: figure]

Der Ausgang, an dem der Widerstand angeschlossen ist, ist mit „D12“ bezeichnet. Das ist der Pin mit der Nummer 12. Damit wir nicht im Programm die Nummer verwenden müssen, um die LED ansteuern zu können, „merken“ wir uns den Pin und definieren dafür eine eigene Bezeichnung. Das macht man durch #define <Platzhalter> <Wert>, dass man über die Loop- und Setup-Funktion schreibt. In diesem Fall also:

#define LED 12

Jetzt müssen wir noch konfigurieren, dass dieser Pin als Ausgang genutzt werden soll. Das muss nur einmal beim Starten des ESP ausgeführt werden und wird daher in die Setup()-Funktion geschrieben. Die Funktion, um einen digitalen Ein- oder Ausgang zu konfigurieren ist pinMode(<Pin>, <INPUT/OUTPUT>). Für alle Stellen im Programm, in denen die Pin Nummer benötigt wird, können wir jetzt den Platzhalter eintragen, also:

pinMode(LED, OUTPUT);

Damit „weiß“ das Programm, dass dieser Pin, an den die LED über den Vorwiderstand angeschlossen ist, einen Wert High/Low ausgeben soll. Das müssen wir im nächsten Schritt auf diesen Pin schreiben. Das soll immer wieder passieren, muss also in die loop()-Funktion geschrieben werden.

Wir wollen einen digitalen Wert auf den Ausgang schreiben. Ein digitaler Wert kann nur zwei Zustände haben: an oder aus, HIGH oder LOW, 1 oder 0, true oder false, etc…

Um jetzt einen Ausgang an- oder auszuschalten, verwenden wir diesen Befehl:

digitalWrite(LED, HIGH);

Mit HIGH wird die LED eingeschaltet. Um sie wieder auszuschalten, schreibt man LOW statt HIGH. Eine blinkende LED schaltet sich in festgelegten Abständen immer wieder an und aus. Um diesen Abstand zu programmieren, nutzt man:

delay(<Zeit in Millisekunden>);

Der Befehl delay stoppt das Programm für die angegebene Zeit.

Nutzen Sie die Funktionen, die Sie kennengelernt haben und lassen Sie die LED in regelmäßigen Zeitabständen (z.B. 2 Sekunden) blinken.

## Aufgabe 4: LED durch Taster steuern

Bisher haben wir einen Pin als Ausgang definiert und benutzt. Ebenso wichtig ist es, Eingänge lesen zu können. Bauen Sie dafür diese Schaltung auf und erweitern Sie ihr Projekt aus der vorherigen Aufgabe.

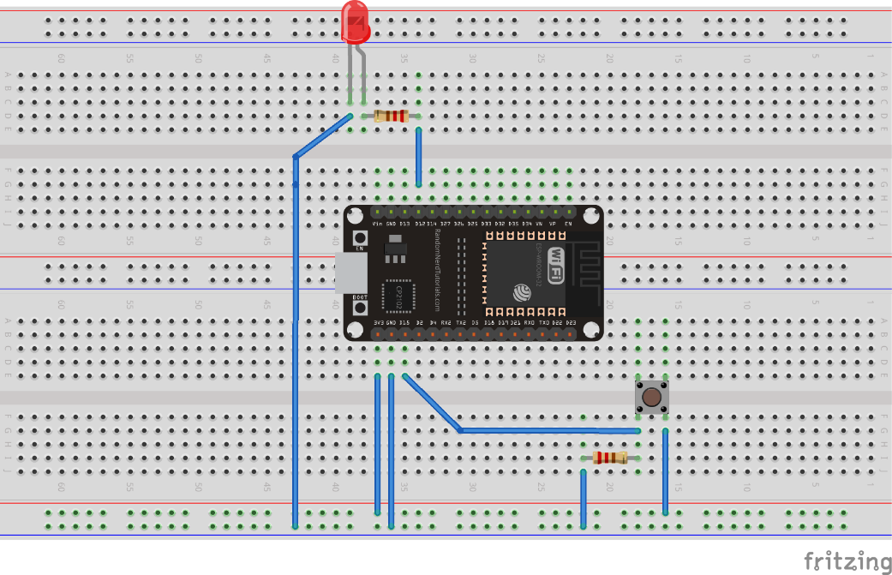
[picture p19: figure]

Die LED ist weiterhin an Pin 12 angeschlossen. Die Konfiguration können wir daher beibehalten. Zusätzlich ist jetzt ein Taster an Pin 15 hinzugekommen. Definieren Sie auch dafür wieder einen Platzhalter und konfigurieren Sie den Pin als Eingang. Verwenden Sie zum definieren das gelernte aus Aufgabe 3.

Jetzt wollen wir lesen, ob der Taster betätigt wird oder nicht. Da dies durchgehend geprüft werden soll, wird auch dies in der loop()-Funktion programmiert. Wir nutzen die Funktion:

digitalRead(<Pin>);

Dafür geben wir an, welchen Pin wir auslesen wollen, die Funktion gibt dann entweder HIGH oder LOW zurück. Diesen Wert speichern wir um ihn anschließend weiterzuverwenden. Dafür legen wir eine Variable an. Variablen sind die Speicher eines Programms und haben immer einen Typ, einen Namen und einen Wert. Der Typ legt fest, was in der Variable gespeichert werden kann. Das Anlegen funktioniert nach dem folgenden Schema:

<Typ> <Name>;

Wenn der Wert der Variable am Anfang schon bekannt ist, kann man diesen auch direkt zuweisen:

<Typ> <Name> = <Wert>;

Die Variable, die wir anlegen muss vom gleichen Typ wie der Rückgabewert der Funktion sein. Zahlenwerte sind meist sogenannte Integer (int), digitale Werte sind boolsche Variablen (bool). Da wir einen digitalen Wert einlesen, erhalten wir entweder HIGH oder LOW.

Wir können die Variable so deklarieren:

bool tasterWert;

Da wir eine Variable nur einmal anlegen müssen macht man dies im Setup.

Um den Wert des Eingangs zu lesen, schreiben wir also:

tasterWert = digitalRead(<Pin>);

Als nächstes müssen wir die LED und den Taster miteinander verbinden. Dabei soll die Regel gelten, dass wenn der Taster gedrückt wird, die LED leuchten soll. In der Programmierung kann man zur Überprüfung von einer Regel die if-Bedingung verwenden. Diese prüft, ob die festgelegte Regel/Bedingung wahr ist.

Beispiel: Wenn es kalt ist, mach die Heizung an. Im Programm würde dies so aussehen:

If(Raum == kalt){

Heizung = an;

}

Eine if-Bedingung kann man sich folgendermaßen vorstellen: Wenn Bedingung erfüllt, dann führe Anweisung1 aus, ansonsten führe Anweisung2 aus.

If(Bedingung){

Anweisung1;

} else {

Anweisung2;

}

Nutzen Sie den Platzhalter, den Sie definiert haben, um den Pin zu lesen. Wie können Sie jetzt den Wert des Tasters mit der LED verbinden?

Tipp: Benutzen Sie als Bedingung ihre Tastervariable.

Hinweis: Mit dem Befehl digitalRead() kann man auch die Signale von einem Liniensensor auslesen.

## Aufgabe 5: LED durch Potentiometer dimmen

Für die Programmierung des Roboters brauchen wir später nicht nur digitale Ein- und Ausgänge, sondern auch analoge. Die können nicht nur HIGH oder LOW sein, sondern mehrere verschiedene (Zahlen-)Werte annehmen.

Um zunächst verschiedene Werte an einem Eingang zu lesen, nutzen wir ein Potentiometer. Das ist ein mechanisch einstellbarer Widerstand. Der Widerstandswert zwischen den beiden äußeren Anschlüssen ist fest. Am mittleren, dritten Anschluss ist der bewegliche Kontakt, dessen Widerstand man durch Drehen verstellen kann. Wenn man an die äußeren Anschlüsse eine Spannung anlegt, erhält man einen einstellbaren Spannungsteiler. Was das bedeutet, können wir mit einem Multimeter anschauen. Bauen Sie dafür die abgebildete Schaltung auf. Dann messen Sie mit einem Multimeter zuerst die Spannung zwischen den äußeren Anschlüssen des Potentiometers, die bleibt immer konstant, auch wenn Sie am Potentiometer drehen. Jetzt messen Sie zwischen dem mittleren Anschluss und dem Ground-Anschluss.

Was passiert, wenn Sie am Potentiometer drehen?

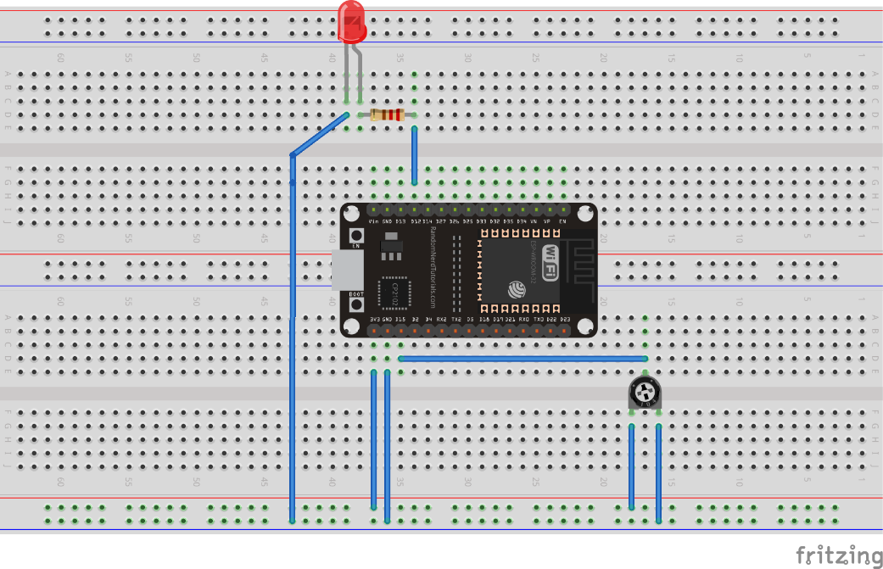
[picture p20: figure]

Die Gesamtspannung an den äußeren Anschlüssen teilt sich entsprechend des Widerstandsverhältnisses auf. Wenn Sie durch Drehen den Widerstand verändern, verändert sich auch die Spannung, die über dem Teil-Widerstand abfällt. Das können wir auch am Anschluss des ESP32 messen und für unser Programm nutzen.

Die Funktion, die wir dafür nutzen lautet

analogRead(<Pin>);

Diese liest den analogen Eingang aus, wie bei der vorherigen Aufgabe kann man den Wert auch in einer Variablen speichern. Dieser Rückgabewert ist vom Typ int. Die Funktion analogRead()kann Werte zwischen 0 und 4095 einlesen.

Jetzt wollen wir durch das Drehen des Potentiometers eine LED mehr oder weniger stark leuchten lassen. Dafür nutzen wir die Funktion:

analogWrite(<Pin>, <Wert>);

Mit analogWrite() kann man 256 verschiedene Helligkeiten einer LED einstellen, angefangen mit 0 für aus und 255 für volle Stärke.

Wie Sie vielleicht bemerkt haben können wir 4096 verschiedene einlesen aber nur 256 Werte ausgeben. Um diese jetzt miteinander verbinden zu können verwendet man den Befehl map().

Der Befehl wird so verwendet:

map(analogRead(<Pin>),0,4096,0,255);

Versuchen Sie den Befehl selbst nachzuvollziehen oder nehmen Sie das Cheatsheet zur Hilfe.

Wichtig: Man kann einen Pin nicht mit digitalWrite() und analogWrite() innerhalb eines Programmes ansteuern.

Hinweise: Mit analogWrite() kann man auch die Geschwindigkeit eines Motors steuern! Der Befehl map() wird auch bei der Verwendung der Lichtsensoren benötigt.

## Aufgabe 6: Beeper ansteuern

Genauso, wie sie in der vorherigen Aufgabe die LED über einen analogen Wert angesteuert haben, können Sie zum Beispiel auch einen „Beeper“, das ist ein kleiner Lautsprecher, ansteuern.

Um den Ton des Beeper verändern zu können, brauchen wir einen neuen Befehl: ledcWrite(<Pin>,<Wert>)

Mit diesem ist es möglich im Gegensatz zu analogWrite() die Frequenz des Signals zu ändern, wodurch sich der Ton ändert. Um ledcWrite() verwenden zu können, müssen wir den Pin zusätzlich zum pinMode()mit ledcAttach(<Pin>,<Frequenz>,8) im Setup initialisieren.

Der Ton verändert sich, wenn Sie eine andere Frequenz nutzen. Probieren Sie verschiedene Frequenzen aus – welcher Ton ist am angenehmsten für Sie? Merken Sie sich diesen Wert, den Beeper brauchen wir später als Hupe für den Roboter!

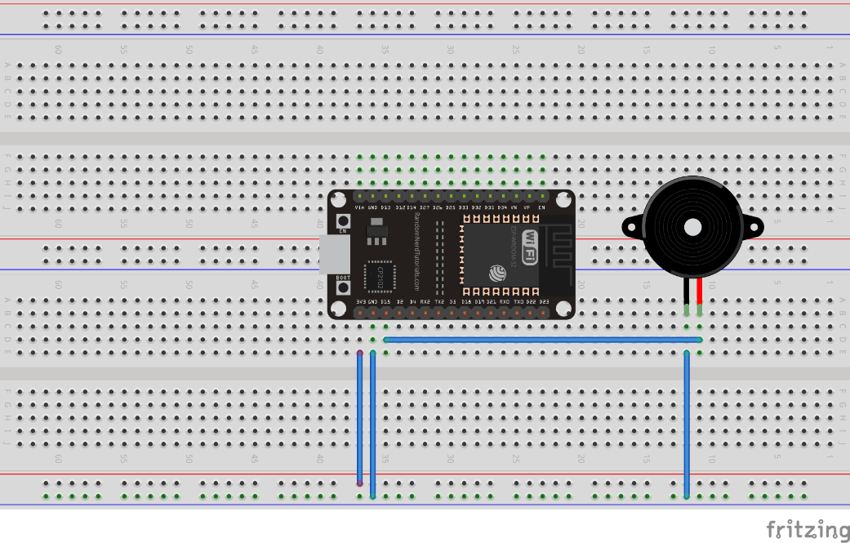
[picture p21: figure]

- Erweiterungen:
  - Frequenz für Beeper in Seriellem Monitor ausgeben
  - LED Schalten nicht tasten
- Cheat Sheet
- Einbinden von Bibliotheken
- #include<Dateiname>
- Übersicht der Standardbefehle unter https://www.arduino.cc/reference/de/

Praktikum Linienroboter – Teil 1

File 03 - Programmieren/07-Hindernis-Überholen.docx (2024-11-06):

# Praktikum Linienroboter

Teil 7: „Hindernis überholen“

Version 1, 06.01.2022

Jetzt nutzen Sie die Linien- und den Hindernissensor in Kombination, um ein Hindernis zu überholen. Bauen Sie dafür als erstes mit drei Linien auf dem Boden eine zweispurige Straße auf.

Der Roboter fährt zunächst zwischen zwei Linien auf der rechten Spur. Wenn ein Hindernis auf der eigenen Spur erkannt wird, soll der Roboter in ausreichendem Abstand halten. Wenn das Hindernis entfernt wird, kann er weiterfahren. Andernfalls soll das Hindernis überholt werden. Dafür muss der Roboter die Mittellinie der Straße überfahren und dann auf der linken Fahrspur eine Zeit lang geradeaus fahren. Anschließend überfährt der Roboter wieder die Mittellinie, um in die rechte Fahrspur zurückzufahren.

Wenn während des Überholvorganges ein Hindernis auf der linken Spur erkannt wird, soll der Roboter hupen und anhalten. Wird das Hindernis entfernt, kann der Roboter weiterfahren und den Überholvorgang fortsetzen.

Bei den Spurwechseln sollen die Blinker passend gesetzt werden.

Auf der nächsten Seite sind die Schritte noch einmal grafisch erklärt.

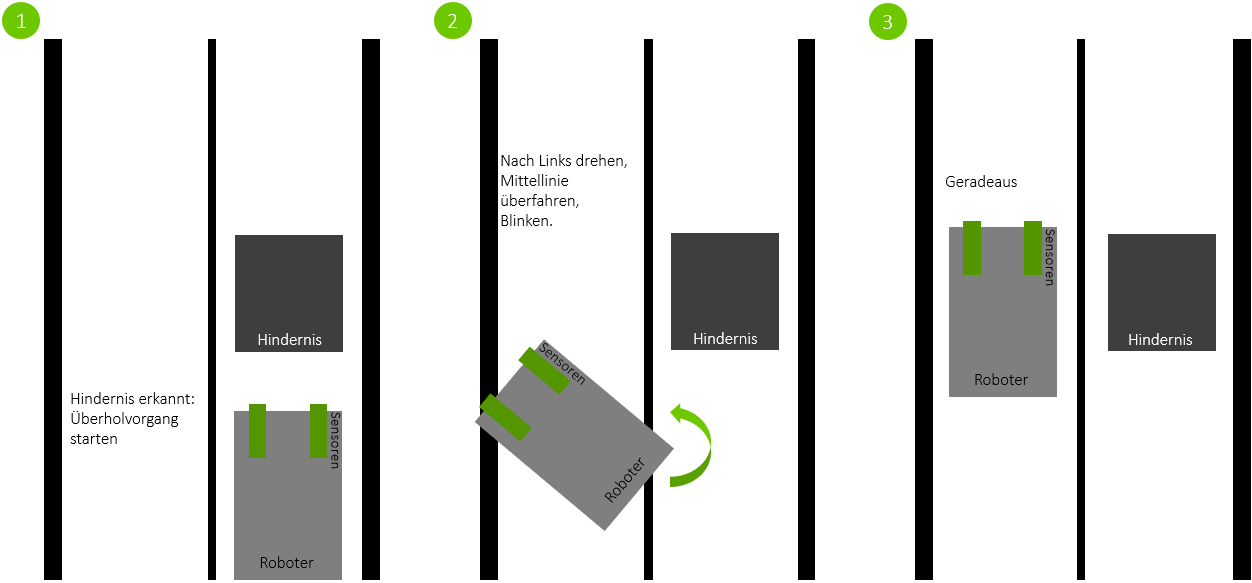
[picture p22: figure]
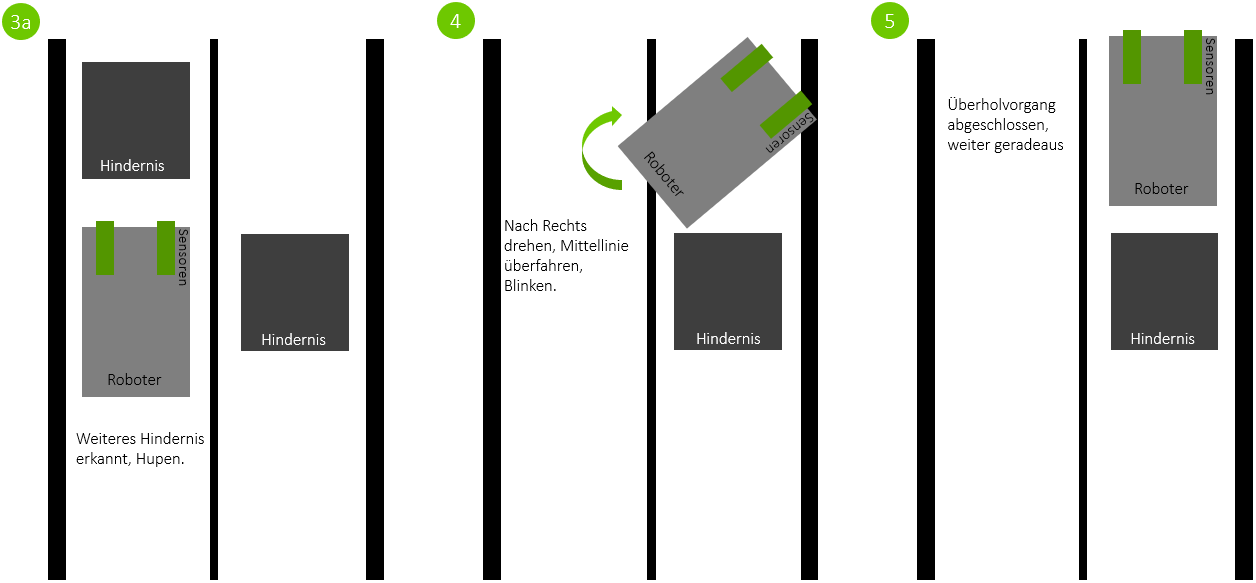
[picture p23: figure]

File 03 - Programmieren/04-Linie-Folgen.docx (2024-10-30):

# Praktikum Linienroboter

Teil 4: „Linie folgen“

Version 1, 06.01.2022

ACHTUNG:

Die Steckbrücke auf dem 2-poligen Stecker, also der Jumper, muss immer abgezogen werden, wenn der ESP32 über ein USB-Kabel mit Ihrem PC verbunden ist! Sind die Batterie und der ESP32 gleichzeitig angeschlossen an die Bauteile kann das zu Problemen führen!

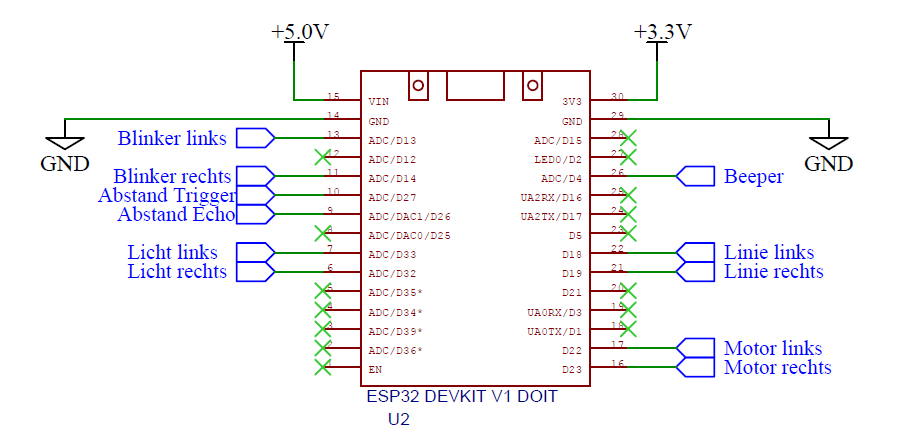
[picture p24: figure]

Obenstehend sehen sie eine Abbildung der Pins des ESP32. In blau eingezeichnet sind die einzelnen Bauteile des Roboters, verbunden mit den jeweiligen Pins. Im Programm müssen sie die Pins auch entsprechend mit den Bauteilen verknüpfen, also die Pins entsprechend definieren mit dem Befehl:

#define <Bezeichnung> <PinNummer>

Dies ist Platinen bedingt und kann nicht geändert werden. Die Pin-Nummer ist hierbei die Zahl die in dem Kasten steht, also bei „Blinker links – D13“ ist die Pin-Nummer 13. Die Zahl außerhalb von dem Kasten ist hier nicht zu beachten.

Theoretisch ließe sich das Programm auch nur durch Pin-Nummer umsetzen, allerdings ist es mit den alternativen-Bezeichnungen viel übersichtlicher.

## Aufgabe 1: "Linie Folgen“

Kombinieren Sie die vorherigen Aufgaben so, dass Ihr Roboter einer Linie folgen kann.

Als Linie funktioniert dünnes, schwarzes Klebeband oder Isolierband das auf einem weißen Tisch im Kreis gezogen wurde.

Die Linie wird schwarz auf weiß sein, also geben die Sensoren ‚HIGH‘ aus, wenn sie über einer Linie sind.

## Aufgabe 2: Blinken

Nutzen Sie die LEDs auf der Platine als Blinker des Roboters. Es soll die linke LED blinken, wenn der Roboter eine Linkskurve fährt und umgekehrt.

## Aufgabe 3: Hupen

Nutzen Sie den Beeper als Hupe des Roboters. Wenn beide Liniensensoren die Farbe der Linie erkennen, soll die Hupe „betätigt“ werden und der Roboter stoppen.

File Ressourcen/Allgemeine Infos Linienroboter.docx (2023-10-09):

Dieser Roboter ist die Grundlage für Schülerpraktika zu den Ingenieursstudiengängen. Dieses Praktikumsprojekt ist im Rahmen einer Bachelorarbeit konzeptioniert und entwickelt worden.

Ziel ist, Spaß an Technik und das Interesse an einem technischen Studium zu fördern. Da wir verschiedene Ingenieursstudiengänge anbieten, bildet das Praktikum in verschiedenen Aufgaben die unterschiedlichen Bereiche ab. Aufgrund der verschiedenen möglichen Studiengänge bei WAGO haben die PraktikantInnen verschiedene Interessensgebiete. Das Praktikum ist so flexibel, dass verschiedene Schwerpunktthemen möglich sind. Da SchülerInnen aus unterschiedlichen Jahrgängen und mit unterschiedlichem Vorwissen unterschiedlich lange Praktika bei uns absolvieren, müssen wir zeitliche Skalierbarkeit gewährleisten. Das bilden wir über modulare Aufgabenstellungen ab.

Die PraktikantInnen erhalten einen Bausatz, aus dem sie im Praktikum einen kleinen, fahrenden Roboter aufbauen und löten. Der Roboter wird über einen ESP32-Mikrocontroller gesteuert. Zunächst lernen die PraktikantInnen die Grundlagen der Programmierung des Mikrocontroller kennen und lernen bspw., die Motoren anzusteuern. Dann erfolgt der Aufbau des Roboters. Anschließend sind abhängig von den Interessen der SchülerInnen verschiedene Aufgaben möglich:

- Im Themenfeld Elektrotechnik werden verschiedene Sensoren angebunden, sodass verschiedene Funktionalitäten (Linie Folgen, Licht Folgen, Vor Hindernissen Halten) mit Hardware-naher Programmierung umgesetzt werden können.
- Im Themenfeld Informatik programmieren die SchülerInnen einen kleinen Webserver, über den der Roboter bspw. vom Handy ferngesteuert werden kann.
- Beim Themenfeld Maschinenbau liegt der Schwerpunkt auf der Konstruktion. Hier erhalten die SchülerInnen einen Grundkurs in einem CAD-Programm und konstruieren anschließend eine eigene Karosserie für ihren Roboter.


Für SchülerInnen, die ein mehrwöchiges Praktikum absolvieren, sind Kombinationen der Aufgaben möglich.

Praktikumsprojekt Roboter

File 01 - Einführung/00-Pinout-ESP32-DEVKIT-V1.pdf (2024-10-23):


23.10.2024 | Internal

Pinout ESP32 DEVKIT V1

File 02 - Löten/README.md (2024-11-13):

# Praktikum "Linien Roboter" - Löten

Version: V1.1  
Dauer: ~2 Wochen  
Bachelor Projekt von Lisa Lueder  
Anpassungen durch Christian Dück und Finn Erik Hilgers  

## Content

Bau- und Lötanleitung des Roboters.

02-Lötanleitung
    Anleitung zur Reihenfolge des Lötens und den Positionen der einzelnen Komponenten auf der Platine

03-Aufbau
    Hinweise und Tipps zum restlichen Aufbau, bezüglich des ESPs, der Räder und der Halbkugeln an den Liniensensoren

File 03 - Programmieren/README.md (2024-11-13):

# Praktikum "Linien Roboter"

Version: V1.1  
Dauer: ~2 Wochen  
Bachelor Projekt von Lisa Lueder  
Anpassungen durch Christian Dück und Finn Erik Hilgers  

## Content

Verschiedene Programmieraufgaben für den Linienroboter.

04-Linie Folgen
    Standardprogramm zur Verfolgung einer Linie auf dem Tisch

05-Licht Folgen
    Programm zur Verfolgung von höheren Lichteinfallen, basierend auf Vergleichen der Photowiderstände

06-Hindernis Erkennung
    Programm zur Ansteuerung des Abstandsensors, und zum Anhalten als reaktion auf auftauchende Objekte
    
07-Hindernis Überholen
    Kombination aller vorheriger Aufgaben, fahren entlang einer Straße und Ausführen eines Überholmanövers als Reaktion auf das Auchtauchen von Objekten.

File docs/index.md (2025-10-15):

---
layout: page
title: Linienroboter
lang: de
lang-ref: index
---

## Kurzer Überblick

Hallo und Willkommen zum Praktikum bei WAGO. In diesem Modul geht es darum, einen Linienroboter aufzubauen. Dieser kann, wie der Name vermuten lässt, einer Linie folgen.
Je nach Umfang des Praktikums können aber auch weitere Funktionen, wie das Überholen eines Hindernisses oder das Folgen einer Taschenlampe implementiert werden.
Dazu muss der Roboter zunächst montiert und gelötet werden, um anschließend die genannten Funktionen programmieren zu können.
Bei Problemen oder Rückfragen kannst du dich gerne an unsere [Ansprechpartner](#ansprechpartner) wenden.

Beispielbild Linienroboter

## Inhaltsverzeichnis
0. [Startseite](index.html)
1. [Einführung](Einfuehrung.html)
   + [Aufgabe 1](Einfuehrung.html#aufgabe-1)
   + [Aufgabe 2](Einfuehrung.html#aufgabe-2)
   + [Aufgabe 3](Einfuehrung.html#aufgabe-3)
   + [Aufgabe 4](Einfuehrung.html#aufgabe-4)
   + [Aufgabe 5](Einfuehrung.html#aufgabe-5)
   + [Aufgabe 6](Einfuehrung.html#aufgabe-6)
2. [Aufbauanleitung](Aufbauanleitung.html)
3. [Linie folgen](Linie-folgen.html)
4. [Licht folgen](Licht-Folgen.html)
5. [Hindernis erkennen](Hindernis-Erkennung.html)
6. [Hindernis überholen](Hindernis-ueberholen.html)
7. [Webserver](Webserver.html)

## Ansprechpartner

- [André Bell](mailto:Andre.Bell@wago.com)
- [Tobias Lauxtermann](mailto:Tobias.Lauxtermann@wago.com)
- [Maik Rehburg](mailto:Maik.Rehburg@wago.com)

<div style="text-align:right"><a href="./Einfuehrung.html">Einführung -></a></div>

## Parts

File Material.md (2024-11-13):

# Material Praktikum

## Teil 1: Einführungsaufgaben
-	Steckbrett
-	ESP32
-	Mikro-USB Kabel
-	Leitungsbrücken male-male
-	LED 5mm, rot
-	2x 220R
-	Mikro-Taster
-	Potentiometer
-	Beeper

## Teil 2: Aufbau und Löten
-	Platine
-	Batterie 9V
-	Batterie-Clip
-	Roter + schwarzer Schaltdraht
-	2x Liniensensor
-	2x Motor
-	2x Transistor BD135
-	2x 180R
-	1x 200R
-	2x 220R (aus Aufgabe 1)
-	1x 390R
-	2x 470R
-	2x 10k
-	Kondensator 1x Tantal 100nF
-	Kondensator 1x Tantal 330nF
-	Kondensator 1x Elko 1µF
-	3x Diode 1N4007
-	2x LEDs gelb
-	Abstandsbolzen
-	2x Buchsenleiste 1x15
-	Schiebeschalter
-   Photowiderstände
-	Ultraschall-Abstandssensor HC-SR04
-	Spannungsregler L7805
-	Steck-Jumper
-	Stiftleiste 2-polig

## Werkzeug und anderweitige Material
-   Lötzubehör
-   Heißluftfön
-   doppelseitiges Klebeband
-   Kabelbinder
-   Schrumpfschlauch
-   Ggfs. 3D-Halbkugel zum Gleiten
-   Reifen

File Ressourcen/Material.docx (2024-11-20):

# Material Praktikum

# Einführungsaufgaben

Menge | Material
1 | Steckbrett
1 | ESP32
1 | Mikro-USB Kabel
1 | LED 5mm, rot
2 | Widerstand 220Ω
1 | Mikro-Taster
1 | Potentiometer
1 | Beeper

# Werkzeug und anderweitiges Material

Menge | Material
1 | Lötzubehör
1 | Doppelseitiges Klebeband
2 | Kabelbinder
1 | Schrumpfschlauch
1 | Heißluftföhn

# Aufbau und Löten

Menge | Material
1 | ESP32
1 | Platine
1 | Batterie 9V
1 | Batterie-Clip
2 | Roter Schaltdraht
2 | Schwarzer Schaltdraht
3 | Leitungsbrücken female - female
2 | Liniensensor
2 | Motor
2 | LED 5mm, gelb
1 | Abstandssensor HC-SR04
2 | Widerstand 180Ω
2 | Widerstand 200Ω
2 | Widerstand 220Ω
2 | Widerstand 390Ω
2 | Widerstand 470Ω
2 | Widerstand 10kΩ
1 | Kondensator Tantal 100nf
1 | Kondensator Tantal 330nf
1 | Kondensator Elko 1µF
3 | Diode 1N4007
2 | Transistor BD135
2 | Photowiderstände
4 | Abstandsbolzen, mittel
1 | Abstandsbolzen, lang
2 | Buchsenleisten 1x15
1 | Buchsenleiste 1x4
1 | Schiebeschalter
1 | Spannungsregler L7805
1 | Steck-Jumper
1 | Stiftleiste 2-polig
1 | 3D-Halbkugel
2 | Reifen
1 | Beeper

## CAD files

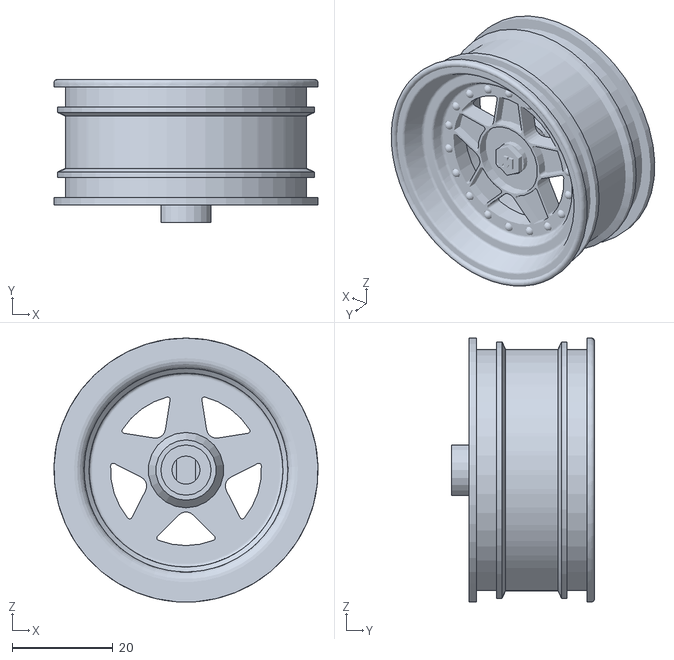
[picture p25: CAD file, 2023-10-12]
Ressourcen/3D-Druck/AW1082-02-62-50-000_Felge_V1.stl
52.5 x 28.5 x 52.5

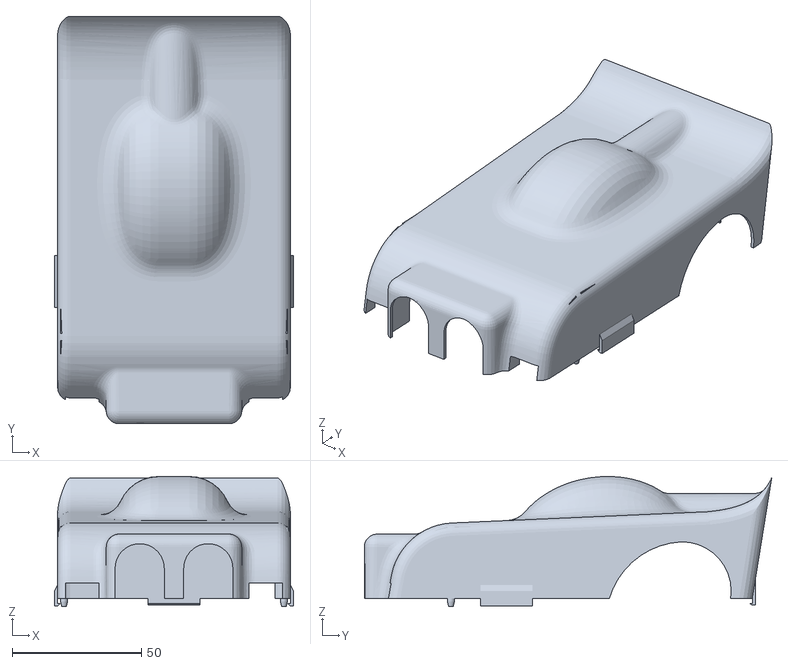
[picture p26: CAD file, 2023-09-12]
Ressourcen/3D-Druck/Karosserie/V3/Chassis_V3_Drucken.stl
92.4 x 157.5 x 50.3

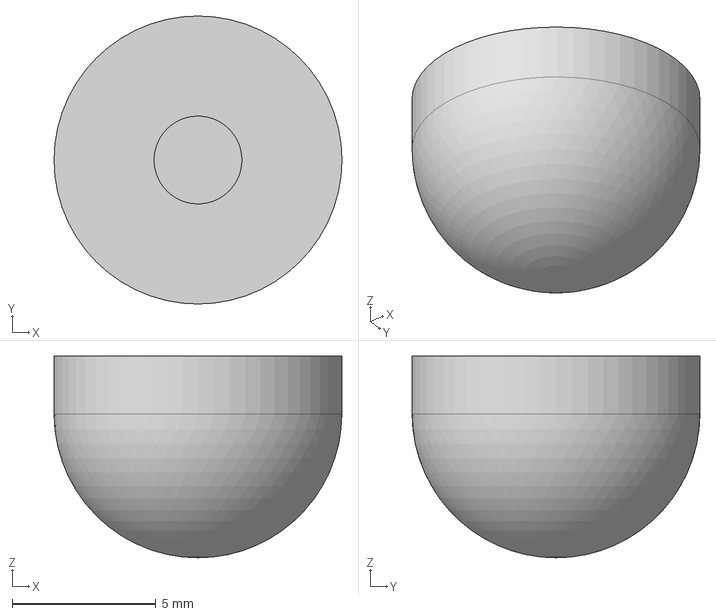
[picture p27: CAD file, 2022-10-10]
Ressourcen/3D-Druck/Halbkugel 1cm Durchmesser - Praktikanten Projekt v1.step
10.0 x 10.0 x 7.00 mm

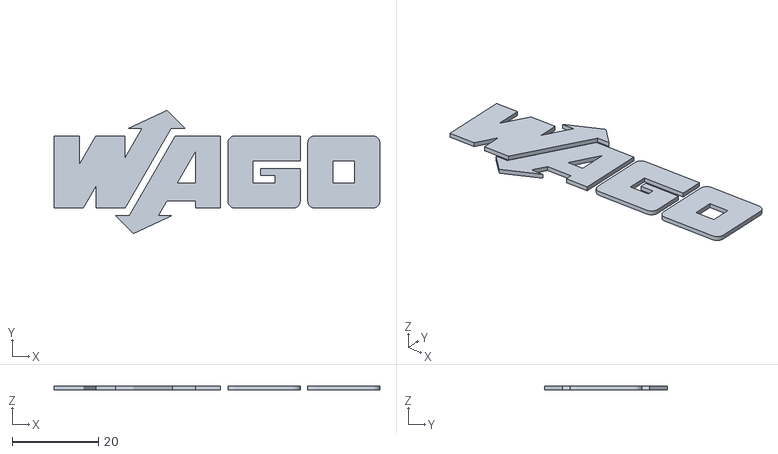
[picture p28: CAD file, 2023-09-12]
Ressourcen/3D-Druck/Karosserie/V3/Schriftzug_V3_Zweifarig_Drucken.stl
75.6 x 28.6 x 1.00

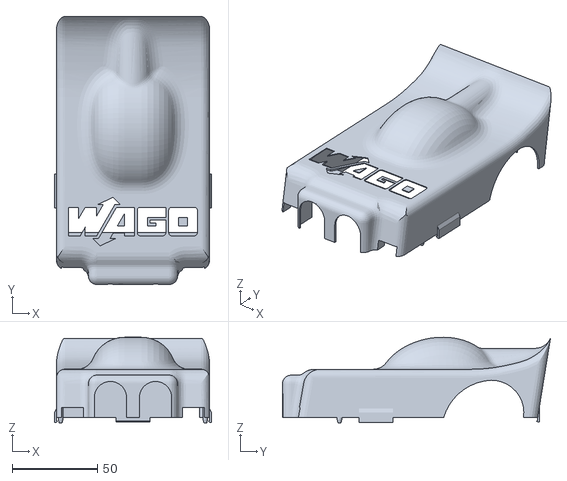
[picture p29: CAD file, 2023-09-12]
Ressourcen/3D-Druck/Karosserie/V3/Chassis_V3_Zweifarig_Drucken.stl
92.4 x 157.5 x 50.3

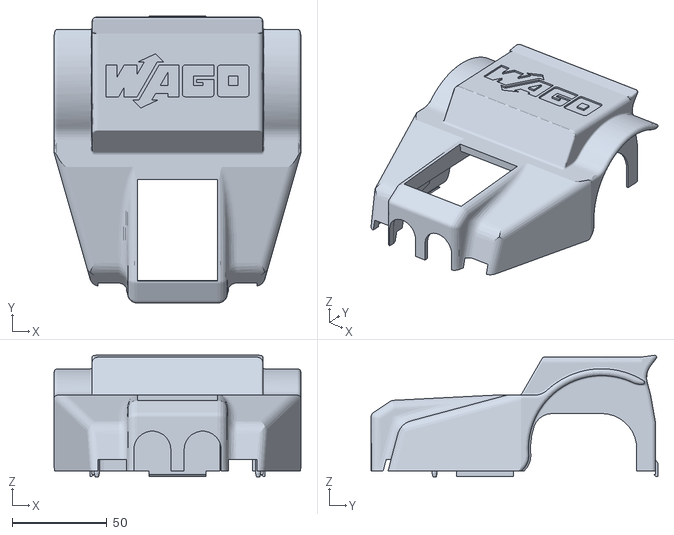
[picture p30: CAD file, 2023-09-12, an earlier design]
Ressourcen/3D-Druck/Karosserie/V1/Chassis_V1_Drucken.stl
130.0 x 151.2 x 64.0

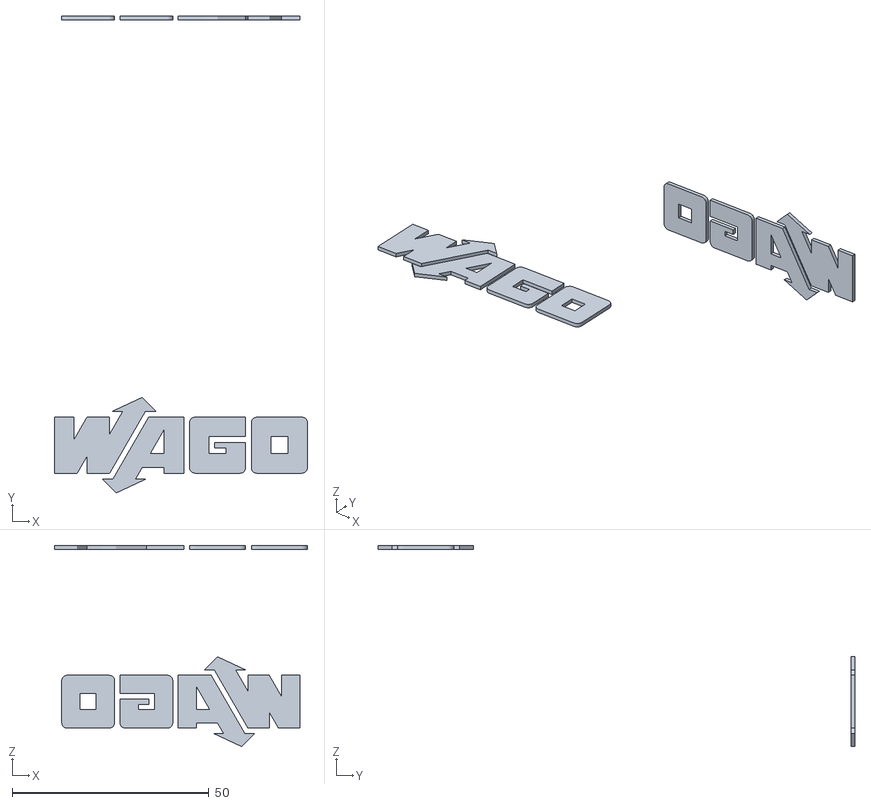
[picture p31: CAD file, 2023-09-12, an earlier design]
Ressourcen/3D-Druck/Karosserie/V2/Schriftzug_V2_Drucken.stl
64.3 x 121.1 x 51.1

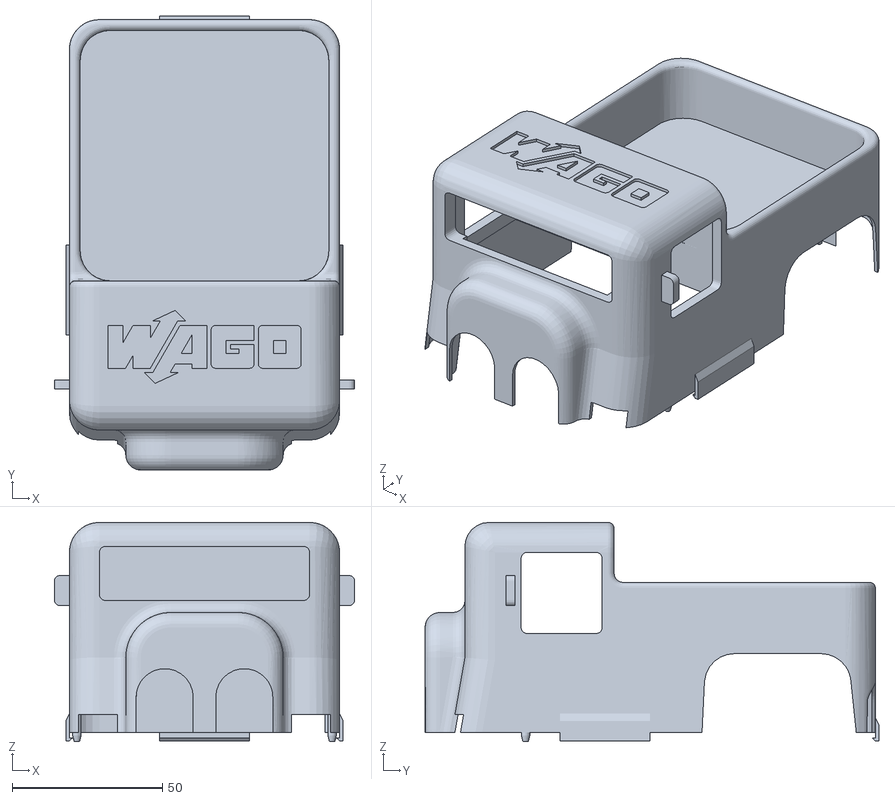
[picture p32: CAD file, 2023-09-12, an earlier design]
Ressourcen/3D-Druck/Karosserie/V2/Chassis_V2_Drucken.stl
100.0 x 151.2 x 73.0

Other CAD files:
Ressourcen/3D-Druck/Karosserie/V1/Schriftzug_V1_Drucken.stl
Ressourcen/3D-Druck/AW1082-02-62-50-000_Felge_V1.prt
Ressourcen/3D-Druck/Halbkugel 1cm Durchmesser - Praktikanten Projekt v1.3mf
Ressourcen/3D-Druck/Halbkugel 1cm Durchmesser - Praktikanten Projekt v1.f3d
Ressourcen/3D-Druck/Karosserie/V1/Chassis_V1_Drucken.prt
Ressourcen/3D-Druck/Karosserie/V2/Chassis_V2_Drucken.prt
Ressourcen/3D-Druck/Karosserie/V3/Chassis_V3_Drucken.prt
Ressourcen/3D-Druck/Karosserie/V3/Chassis_V3_Zweifarig_Drucken.prt

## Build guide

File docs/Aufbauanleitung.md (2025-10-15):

---
layout: page
title: Linienroboter - Montage
lang: de
lang-ref: index
---
## Aufbauanleitung
Diese Anleitung soll dich durch den gesamten Aufbauprozess des Roboters führen. Damit dieser möglichst geordnet abläuft solltest du auch hier zunächst prüfen, ob [du alle Bauteile hast](Material.pdf).
### Löten

>:exclamation:  
>Bevor du mit dem Löten startest, wende dich an einen [Betreuer](./index.html/#ansprechpartner), damit wir dir eine kurze Einführung und Sicherheitseinweisung zum Löten erteilen können.

|Vorderseite|Rückseite|
|:---:|:---:|
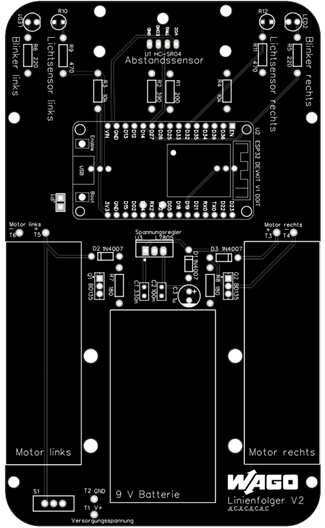
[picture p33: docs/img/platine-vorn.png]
Vorderseite der Platine
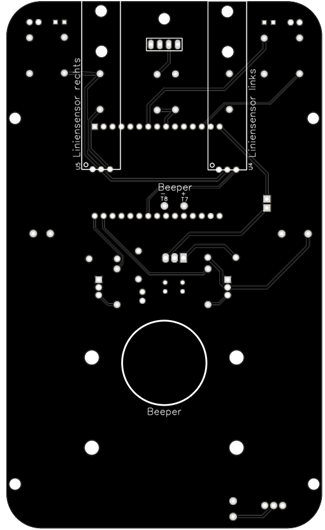
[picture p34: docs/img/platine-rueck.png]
Rückseite der Platine
|||

Das ist die Platine des Linienroboters. Jede weiß umrandete Fläche steht für ein eigenes Bauteil, welches auf der Platine angelötet werden soll. Die Markierungen einzelner Bauteile entsprechen auch den Markierungen auf der Platine, also muss z.B. die LED auch entsprechend der Kerbe auf der Platine angeordnet werden.

{: .info}
Beim Löten empfiehlt es sich, nicht direkt alle Bauteile anzulöten, sondern nach deren Größe sortiert. Sonst könnten kleinere Bauteile wieder herausrutschen, wenn man die Platine umdreht.

Am besten geht man nach folgender Schritt-für-Schritt-Anleitung vor:

1. Widerstände und Dioden
   + Biege die Anschlussdrähte zunächst zu den Löchern auf der Platine passend
   + Achte bei den Dioden auf jeden Fall darauf, dass sie richtig gepolt eingebaut werden - der Ring auf der Diode muss mit dem auf der Platine übereinstimmen
   + Die Widerstände müssen vorher mit einem Multimeter geprüft werden
2. Kondensatoren C1 & C2
   + Auch hier ist die Einbaurichtung entscheidend
   + Das auf des Bauteil gedruckte `+` muss in Fahrtrichtung zeigend eingebaut werden
3. Batteriehalter
   + Roter Anschlussdraht an `+`, schwarzer an `GND`
4. LEDs
   + Entsprechend der auf der Platine angezeigten Polung
5. Schalter S1
6. Beeper
   + Rot an `+`, schwarz an `-`
   + Klebe den Beeper später mit Klebeband an der Platine fest
7. Liniensensoren
   + Schneide die 3-er Leitungsbrücken in der Mitte durch und isoliere sie etwas ab
   + Die Metallstifte des Sensors werden nachher übereinstimmend mit den Lötstellen angeschlossen. Löte die Kabel also in einer beliebigen Reihenfolge an
   + Wenn du alles fertig gelötet hast, kannst du die Liniensensoren mit den mittleren Abstandshaltern an der Platine anbringen
8. Buchsenleisten
   + Löte diese auf jeden Fall parallel zueinander an, damit der ESP32 nachher problemlos montiert werden kann
9. Kondensator C3
10. 2-Pol-Steckerleiste (Jumper)
    + Die kurzen Enden müssen auf die Platine gelötet werden
11. Transistoren
    + Die beschriftete (Vorder-)seite des Transistors muss in Richtung des Punktes auf der Platine weisen
12. Fotowiderstände R10 & R12
    + Lasse sie etwas überstehen
13. Spannungswandler
    + Auch hier muss die Vorderseite wieder dem Punkt zugewandt sein
14. Motoren
    + Löte je ein rotes und ein schwarzes Kabel an die Platine
    + Um die Drehrichtung des Motors noch ändern zu können löte die Kabel erst nach den ersten Tests am Motor an

### Aufbau
+ Baue die Liniensensoren an (s.O.)
+ Baue mit dem längeren Abstandshalter die 3D-Kugel an. Achte dabei darauf, dass der Abstandhalter die passende Gewindestärke hat
+ Befestige die Motoren und die Batterie mit Kabelbindern am Roboter
+ Stecke den ESP32 auf die 15-poligen Buchsenleisten
+ Bestfestige die Räder an den Motoren
+ Stecke den Abstandssensor in die vordere Buchsenleiste

| | |
|:---|---:|
|<a href="./Einfuehrung.html"><- Einführung</a>|<a href="Linie-folgen.html">Linie folgen -></a>|

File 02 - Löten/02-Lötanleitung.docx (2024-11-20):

# Praktikum Linienroboter

Teil 2: Lötanleitung

Version 1.2, 06.11.2024

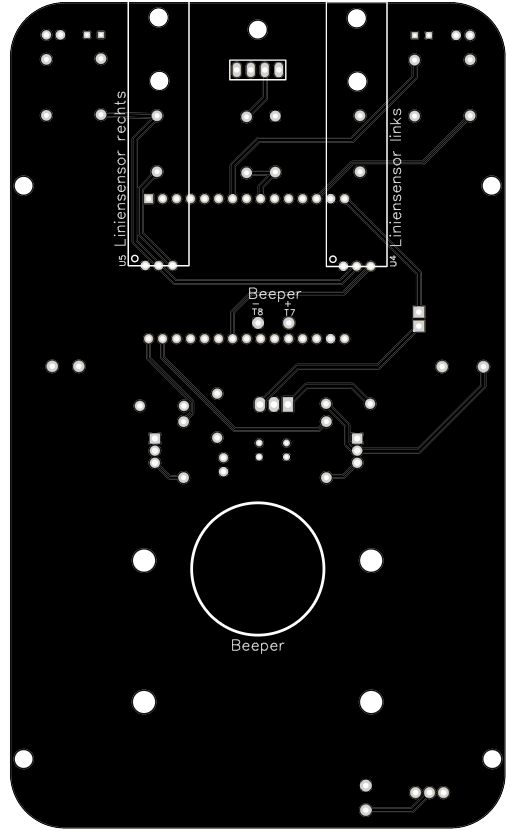
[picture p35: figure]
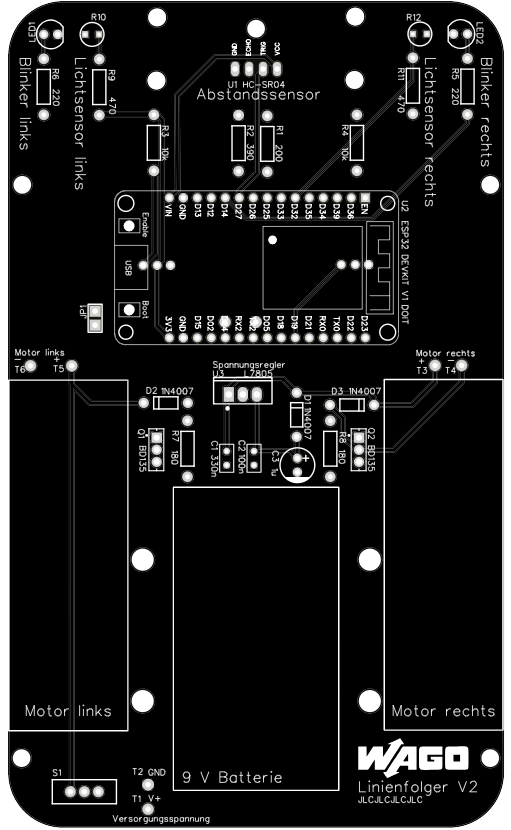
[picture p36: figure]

Abgebildet sehen sie die Platine des Linienroboters. Jede weiß umrandete Fläche steht für ein eigenes Bauteil, welches auf der Platine angelötet werden soll. Die Markierungen einzelner Bauteile entsprechen auch den Markierungen auf der Platine, also muss z.B. die LED auch entsprechend der Kerbe auf der Platine angeordnet werden.

Einige weitere Hinweise zum Aufbauen des Roboters:

- Starten Sie mit den „flachsten“ Komponenten und arbeiten sich zu den höheren vor:
  1. Widerstände und Dioden.
    - Biegen Sie die Anschlussdrähte erst passend, sodass die Bauteile an die Lötstellen passen.
    - Achten Sie bei den Dioden auf die richtige Anschlussrichtung! Die silberne Markierung auf dem Bauteil muss zu dem markierten Teil auf der Platine passen.
    - ACHTUNG! MESSEN SIE DIE WIDERSTÄNDE BEVOR SIE DIESE VERWENDEN!
  2. Kondensatoren C1 und C2
    - Achten Sie auch hier auf die passende Richtung. Auf den Kondensatoren steht ein kleines „+“. Das muss an den Anschluss, der auf der Platine nach vorne (in Fahrtrichtung) zeigt.
    - Die Kondensatoren sind klein und gelb, der kleinere von beiden ist der mit 100n, der größere mit 330n.
  3. Anschluss der Batterie
    - Der rote Anschlussdraht muss an „+“, der schwarze an „GND“
  4. LEDs
    - Auch hier muss die Richtung passend gewählt sein. Die abgeflachte Seite des Bauteils ist auf der Platine dargestellt, orientieren Sie sich daran.
  5. Schalter S1
  6. Beeper
    - Auch hier: Rot an „+“, Schwarz an „-“
    - Nutzen Sie doppelseitiges Klebeband, um den Beeper an der markierten Position zu befestigen
  7. Liniensensoren
    - Schneiden Sie drei Jumper mit Buchsen-Anschlüssen an beiden Seiten in der Mitte durch und isolieren Sie ein Stück weit ab. Das Ende mit dem Buchsen-Anschluss dient als Verbindung zum Sensor und wird aufgesteckt. Das andere Ende löten Sie an die Platine.
    - Die Darstellung auf der Platine ist genau passend zum Sensor, das heißt die Metallstifte des Sensors werden mit genau der darunter liegenden Lötstelle verbunden.
    - Wenn die Jumper verbunden sind, nutzen Sie je einen oder zwei Abstandshalter, um den Sensor zu befestigen. Diese müssen sie an die Platine schrauben. Die erste Bohrung am vorderen Rand eignet sich am besten.
  8. Buchsenleisten
    - Sie haben in Ihrem Bausatz Buchsenleisten, auf die Sie später das ESP32-Board und den Ultraschallsensor stecken. Passen sie die Länge an, wenn nötig.
    - Achten Sie beim Löten darauf, dass die Buchsenleisten gerade sind. Ansonsten können Sie den ESP und den Ultraschallsensor nicht richtig darauf stecken!
  9. Kondensator C3
    - Hier ist wieder eine silberne Markierung auf dem Bauteil. Diese muss passend zu der Markierung auf der Platine sein.
  10. 2-Pol Steckerleiste (Jumper/JP)
    - Kürzen Sie die Steckerleiste auf 2-Pole. Die kurzen Enden werden auf die Platine gelötet. Auf die langen Enden wird später eine Steckbrücke gesteckt.
  11. Transistoren Q1 und Q2
    - Die „Vorderseite“ dieser Bauteile ist die schwarze, die auch beschriftet ist. An dem Kästchen auf der Platine sehen Sie an einer Ecke einen kleinen Punkt. Dieser Punkt markiert „den ersten Pin“ des Bauteils. In diesem Fall heißt das, dass die Vorderseite in Richtung des Punktes zeigen muss.
  12. Fotowiderstände R10/R12
    - Die Fotowiderstände sollten ca. 1-2 cm über der Platine überstehen. Achten Sie darauf, dass beide ungefähr die gleiche Höhe haben.
  13. Spannungswandler U3
    - Auf der Platine ist wieder mit einem Punkt der „erste“ Pin gekennzeichnet. Die Vorderseite ist auch hier wieder die beschriftete Seite. Hier muss also die Vorderseite des Bauteils zum hinteren Ende des Roboters zeigen.
  14. Motoren
    - Löten sie jeweils einen roten und einen schwarzen Anschlussdraht an jeden Motor. Dabei sollten die Drähte bei jedem Motor auf jeweils der anderen Seite sein, d.h. Wenn Beide Motoren nebeneinander liegen, soll bei einem der rote Draht links und bei dem anderen rechts sein, entsprechend andersherum bei den schwarzen Drähten.
    - Kleben Sie die Motoren mit doppelseitigem Klebeband an die vorgesehene Position, dabei sollen die roten Drähte nach oben zeigen und die Schrauben nach innen.
    - Nutzen Sie Kabelbinder, um sie zusätzlich an den Bohrungen zu befestigen.
    - Löten Sie dann die Anschlussdrähte an die Platine (rot „+“, schwarz „-“)
  15. Batterie
    - Befestigen Sie zwei weitere Kabelbinder über Kreuz an den Bohrungen, an denen auch die Motoren befestigt sind.
    - Darunter können Sie den Anschlussdraht des Batterie-Clips „verstecken“.
    - Die Batterie kleben Sie mit doppelseitigem Klebeband auf die gekreuzten Kabelbinder. Wenn die Batterie leer ist, ist sie so leichter auszutauschen, als wenn sie direkt auf die Platine geklebt wird.

Praktikum Linienroboter – Teil 3

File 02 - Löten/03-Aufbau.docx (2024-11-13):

Aufbau

Teil 3: Aufbau

Version 1.2, 06.11.2024

ESP 32

Stecken sie den ESP in die zuvor angelöteten Steckbuchsen. Achten sie dabei darauf, dass jedes Beinchen des ESPs auch in der Buchse ist. Sollte der ESP nicht einsteckbar sein, überprüfen sie die Buchsenleisten.

Sind sie parallel zueinander ausgerichtet und gerade?

- Probieren sie sonst diese leicht zu biegen, sodass der ESP hineinpasst.

Stört etwas das Einstecken des ESPs?

- Probieren sie es zur Seite zu schieben oder anders zu platzieren.

Räder

Stecken sie die Räder an die nach außen zeigenden weißen Getriebewellen. Testen sie, ob die Räder auch einigermaßen fest sitzen. Sind die Räder viel zu locker, könnte es nötig sein, diese mit Heißkleber oder Ähnlichem an den Getriebewellen zu befestigen.

Halbkugeln (optional)

Betrachten sie die Liniensensoren. An diesen sehen sie jeweils ein weißes, drehbares Potentiometer. Mit diesem Potentiometer lässt sich die Genauigkeit der Liniensensoren einstellen.

Das Potentiometer schleift beim Betrieb normalerweise über den Boden. Um das zu verhindern wurden Halbkugeln gedruckt, die sie vorne am Roboter befestigen können. Dabei gibt es zwei Optionen:

1:

Schrauben sie den langen Abstandshalter mit einer Schraube vorne an den Roboter, nutzen sie dafür das Loch, dass zwischen Sender und Empfänger des Ultraschallsensors sichtbar ist. Dabei sollte der Gewindeteil nach unten zeigen. Dort können sie nun die Halbkugel draufschrauben

2:

Kleben sie auf den weißen, drehbaren Teil der Potentiometer mit Heißkleber eine Halbkugel, sodass die Flache Seite auf dem Potentiometer klebt. Probieren sie hierbei, dass das Potentiometer immer noch drehbar bleibt.

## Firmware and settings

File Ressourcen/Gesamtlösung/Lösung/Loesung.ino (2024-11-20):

//pin-definitions
#define TURNSIGNALLEFT 13
#define TURNSIGNALRIGHT 14
#define DISTANCETRIGGER 27
#define DISTANCEECHO 26
#define LIGHTLEFT 33
#define LIGHTRIGHT 32
#define BEEPER 4
#define LINELEFT 18
#define LINERIGHT 19
#define MOTORLEFT 22
#define MOTORRIGHT 23

//lineDrive
#define MOTORSPEED 85 //Hoechstgewschwindigkeit
#define MOTORSLOW 50 //Untere Geschwindigkeit
#define TURNCYCLES 15

//followLight
#define LIGHTDIFFERENCE 150

//overtake
#define SWITCHCYCLES 50

//VARIABLES-----------------------------

//lineDrive
int StopCycles = 0;
int StopWarn = 0;
int StopActivate = 0;

int LeftCycles = 0;
bool LeftBrake = false;

int RightCycles = 0;
bool RightBrake = false;

//followLight
int LDRLeftVal = 0;
int LDRRightVal = 0;

//obstacleScan
long Time = 0;
long Distance = 0;
bool Obstacle = false;

//Road
bool IsOvertaking = false;
bool LineLeft = false;
bool LineRight = false;

//Overtake
bool OvertakeMode = false; //If true, car will try to overtake as if on Road. If false, it will just beep if an obstacle is detected
int Case = 0;
int TurnSignalCounter = 0;
int SwitchCounter = 0;

bool LineCount = 0;


void setup() {
  // put your setup code here, to run once:
  Serial.begin(115200);
  pinMode(TURNSIGNALLEFT, OUTPUT);
  pinMode(TURNSIGNALRIGHT, OUTPUT);
  pinMode(DISTANCETRIGGER, OUTPUT);
  pinMode(DISTANCEECHO, INPUT);
  pinMode(LIGHTLEFT, INPUT); //LIGHTSENSOR
  pinMode(LIGHTRIGHT, INPUT); //LIGHTSENSOR
  pinMode(BEEPER, OUTPUT);
  pinMode(LINELEFT, INPUT);
  pinMode(LINERIGHT, INPUT);
  pinMode(MOTORLEFT, OUTPUT);
  pinMode(MOTORRIGHT, OUTPUT);
  ledcAttach(MOTORLEFT, 15000, 8);
  ledcAttach(MOTORRIGHT, 15000, 8);
  ledcAttach(BEEPER, 450, 8);
}

void loop() {
  // put your main code here, to run repeatedly:
  

  obstacleScan();
  if(Obstacle || IsOvertaking){
    if(OvertakeMode){
      overtake();
    } else {
      ledcWrite(BEEPER, 8);
      analogWrite(TURNSIGNALLEFT, 255);
      analogWrite(TURNSIGNALRIGHT, 255);
      ledcWrite(MOTORRIGHT, 0);
      ledcWrite(MOTORLEFT, 0);
    }

  } else {
    // hier wird entschieden welches Programm aktuell ausgeführt werden soll.
    // alle Programme die nicht laufen sollen werden auskommentiert

    lineDrive();
    //followLight();
    //road();
  }
  Serial.println("---------------");
}

void lineDrive(){ //Follow the Line
  if(!digitalRead(LINELEFT) && !digitalRead(LINERIGHT)){ //Full Forward
    analogWrite(TURNSIGNALLEFT, 0);
    analogWrite(TURNSIGNALRIGHT, 0);
    ledcWrite(MOTORLEFT, MOTORSPEED);
    ledcWrite(MOTORRIGHT, MOTORSPEED);
    ledcWrite(BEEPER, 0);
    
    RightBrake = false;
    LeftBrake = false;
    StopActivate = 0;
  }
  
  else if(digitalRead(LINERIGHT) && !digitalRead(LINELEFT)){ //RIGHT
    analogWrite(TURNSIGNALRIGHT, 255);
    analogWrite(TURNSIGNALLEFT, 0);
    ledcWrite(MOTORRIGHT, MOTORSLOW);
    ledcWrite(MOTORLEFT, MOTORSPEED);
    
    if(RightBrake){
      ledcWrite(MOTORRIGHT, 0);
    }
    RightCycles += 1;
    if(RightCycles == TURNCYCLES){
      RightCycles = 0;
      RightBrake = true;
    }

    LeftBrake = false;
    StopActivate = 0;
  }

  else if(digitalRead(LINELEFT) && !digitalRead(LINERIGHT)){ //LEFT
    analogWrite(TURNSIGNALLEFT, 255);
    analogWrite(TURNSIGNALRIGHT, 0);
    ledcWrite(MOTORLEFT, MOTORSLOW);
    ledcWrite(MOTORRIGHT, MOTORSPEED);
    if(LeftBrake){
      ledcWrite(MOTORLEFT, 0);
    }
    LeftCycles += 1;
    if(LeftCycles == TURNCYCLES){
      LeftCycles = 0;
      LeftBrake = true;
    }

    RightBrake = false;
    StopActivate = 0;
  }
  
  else { //STOP
    if(StopActivate >= 1){ //delayed brake
      ledcWrite(MOTORRIGHT, 0);
      ledcWrite(MOTORLEFT, 0);
      ledcWrite(BEEPER, 8);
    }

    if(StopWarn == 5){ //Brake Activator
      StopWarn = 0;
      StopActivate += 1;
      if(StopActivate > 5){
        StopActivate -= 1;
      }
    }
    else if(StopWarn == 1 || StopWarn == 3){ //LIGHTS SWITCHING
      analogWrite(TURNSIGNALRIGHT, 255); //Right on
      analogWrite(TURNSIGNALLEFT, 0);
    }
    else{
      analogWrite(TURNSIGNALLEFT, 255); //Left on
      analogWrite(TURNSIGNALRIGHT, 0);
    }

    StopCycles += 1; //CycleCounter
    if(StopCycles == 15){
      StopCycles = 0;
      StopWarn += 1;
    }
  }
}

void followLight(){ //THE DARKER THE HIGHER THE VAL -> Low = Light
  LDRLeftVal = analogRead(LIGHTLEFT);
  LDRRightVal = analogRead(LIGHTRIGHT)+200;//Compensation for different Values

  if(LDRLeftVal < LDRRightVal){ //Left
    if(LDRRightVal - LDRLeftVal > LIGHTDIFFERENCE){
      ledcWrite(MOTORLEFT, MOTORSLOW);
      ledcWrite(MOTORRIGHT, MOTORSPEED);
      ledcWrite(BEEPER, 8);
      analogWrite(TURNSIGNALLEFT, 255);
      analogWrite(TURNSIGNALRIGHT, 0);
    }
  }
  else if(LDRRightVal < LDRLeftVal){ //Right
    if(LDRLeftVal - LDRRightVal > LIGHTDIFFERENCE){
      ledcWrite(MOTORRIGHT, MOTORSLOW);
      ledcWrite(MOTORLEFT, MOTORSPEED);
      ledcWrite(BEEPER, 8);
      analogWrite(TURNSIGNALRIGHT, 255);
      analogWrite(TURNSIGNALLEFT, 0);
    }
  }
  else{ //Forward
    ledcWrite(MOTORLEFT, MOTORSPEED);
    ledcWrite(MOTORRIGHT, MOTORSPEED);
    ledcWrite(BEEPER, 0);
    analogWrite(TURNSIGNALLEFT, 0);
    analogWrite(TURNSIGNALRIGHT, 0);
  }
}

void obstacleScan(){
  digitalWrite(DISTANCETRIGGER, HIGH); //Send Signal
  delayMicroseconds(10);
  digitalWrite(DISTANCETRIGGER, LOW);
  Time = pulseIn(DISTANCEECHO, HIGH); //Receive Signal
  Distance = (Time / 2) * 0.03432;

  if(Distance < 15){
    Obstacle = true;
  }
  else {
    Obstacle = false;
  }
}

void road(){
  LineLeft = digitalRead(LINELEFT);
  LineRight = digitalRead(LINERIGHT);

  if(!LineLeft && !LineRight){
    analogWrite(TURNSIGNALLEFT, 0);
    analogWrite(TURNSIGNALRIGHT, 0);
    ledcWrite(MOTORLEFT, MOTORSPEED);
    ledcWrite(MOTORRIGHT, MOTORSPEED);
    ledcWrite(BEEPER, 0);
  }
  else if(LineLeft && !LineRight){ //Go RIGHT
    ledcWrite(MOTORLEFT, MOTORSPEED);
    ledcWrite(MOTORRIGHT, MOTORSLOW);
  }
  else if(!LineLeft && LineRight){ //Go LEFT
    ledcWrite(MOTORLEFT, MOTORSLOW);
    ledcWrite(MOTORRIGHT, MOTORSPEED);
  }
  else{
    ledcWrite(MOTORRIGHT, 0);
    ledcWrite(MOTORLEFT, 0);
  }
}

void overtake(){
  if(Obstacle && Case >= 3){
    ledcWrite(BEEPER, 8);
    analogWrite(TURNSIGNALLEFT, 255);
    analogWrite(TURNSIGNALRIGHT, 255);
    ledcWrite(MOTORRIGHT, 0);
    ledcWrite(MOTORLEFT, 0);
  }
  else{
    ledcWrite(BEEPER, 0);
    Serial.println("Case: " + Case);
    switch(Case){
    case 0: //Stop and TurnSignal Left
      IsOvertaking = true;
      ledcWrite(MOTORRIGHT, 0);
      ledcWrite(MOTORLEFT, 0);
      analogWrite(TURNSIGNALLEFT, 255);
      delay(500);
      analogWrite(TURNSIGNALLEFT, 0);
      delay(500);
      analogWrite(TURNSIGNALLEFT, 255);
      delay(500);
      analogWrite(TURNSIGNALLEFT, 0);
      delay(500);
      analogWrite(TURNSIGNALLEFT, 255);
      delay(500);
      analogWrite(TURNSIGNALLEFT, 0);
      delay(500);
      Case += 1;
      break;
    case 1: //Turn Left
      ledcWrite(MOTORRIGHT, MOTORSPEED);
      ledcWrite(MOTORLEFT, 0);
      SwitchCounter += 1;
      if(SwitchCounter > SWITCHCYCLES){
        ledcWrite(MOTORRIGHT, 0);
        ledcWrite(MOTORLEFT, 0);
        Case += 1;
        SwitchCounter = 0;
      }
      break;
    case 2: //Drive Till second line
      // LineLeft = digitalRead(LINELEFT); Linecounting, did not work hence remodelling to Time-based
      // LineRight = digitalRead(LINERIGHT);

      // switch(LineCount){
      //   case 0:
      //     ledcWrite(MOTORRIGHT, MOTORSPEED);
      //     ledcWrite(MOTORLEFT, MOTORSPEED);
      //     if(LineLeft) {
      //       LineCount += 1;
      //     }
      //     Serial.println("LINELEFT 1");
      //     break;
      //   case 1:
      //     ledcWrite(MOTORRIGHT, MOTORSPEED);
      //     ledcWrite(MOTORLEFT, MOTORSPEED);
      //     if(LineRight) {
      //       LineCount += 1;
      //     }
      //     Serial.println("LINERIGHT");
      //     break;
      //   case 2:
      //     if(LineLeft){
      //       ledcWrite(MOTORRIGHT, 0);
      //       ledcWrite(MOTORLEFT, 0);
      //       Serial.println("LINELEFT STOP");
      //       Case += 1;
      //     }
      //   break;
      //}
      ledcWrite(MOTORRIGHT, MOTORSPEED);
      ledcWrite(MOTORLEFT, MOTORSPEED);
      delay(500);
      pulseIn(LINELEFT, HIGH);
      ledcWrite(MOTORRIGHT, 0);
      ledcWrite(MOTORLEFT, 0);
      Case += 1;
      break;

    case 3: //Turn Right (onto road)
      ledcWrite(MOTORLEFT, MOTORSPEED);
      ledcWrite(MOTORRIGHT, 0);
      SwitchCounter += 1;
      if(SwitchCounter > SWITCHCYCLES){
        ledcWrite(MOTORRIGHT, 0);
        ledcWrite(MOTORLEFT, 0);
        Case += 1;
        SwitchCounter = 0;
      }
      break;
    case 4: //Drive for certain time
      ledcWrite(MOTORRIGHT, MOTORSPEED);
      ledcWrite(MOTORLEFT, MOTORSPEED);
      delay(2000);
      Case += 1;
      break;
    case 5: //Turn Right TurnSignal Right
      ledcWrite(MOTORLEFT, MOTORSPEED);
      ledcWrite(MOTORRIGHT, 0);
      analogWrite(TURNSIGNALRIGHT, 255);
      SwitchCounter += 1;
      if(SwitchCounter > SWITCHCYCLES){
        ledcWrite(MOTORRIGHT, 0);
        ledcWrite(MOTORLEFT, 0);
        Case += 1;
        SwitchCounter = 0;
      }
      break;
    case 6: //Drive Till second line
      analogWrite(TURNSIGNALRIGHT, 0);
      ledcWrite(MOTORRIGHT, MOTORSPEED);
      ledcWrite(MOTORLEFT, MOTORSPEED);
      delay(500);
      pulseIn(LINERIGHT, HIGH);
      ledcWrite(MOTORRIGHT, 0);
      ledcWrite(MOTORLEFT, 0);
      Case += 1;
      break;
    case 7: //Turn Left (onto Road)
      ledcWrite(MOTORRIGHT, MOTORSPEED);
      ledcWrite(MOTORLEFT, 0);
      SwitchCounter += 1;
      if(SwitchCounter > SWITCHCYCLES){
        ledcWrite(MOTORRIGHT, 0);
        ledcWrite(MOTORLEFT, 0);
        Case += 1;
        SwitchCounter = 0;
      }
      break;
    case 8: //EndCase
      IsOvertaking = false;
      ledcWrite(MOTORRIGHT, 0);
      ledcWrite(MOTORLEFT, 0);
      break;
    }
  }
}

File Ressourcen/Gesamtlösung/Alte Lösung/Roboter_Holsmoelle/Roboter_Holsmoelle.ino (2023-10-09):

//Einbinden der Biblotheken
#include <WiFi.h>
//#include <HSCR04.h>
//Definieren der Ausgänge
#define BlinkerL 13
#define BlinkerR 14

#define FotowiderstandL 33
#define FotowiderstandR 32

#define LiniensensorL 18
#define LiniensensorR 19

#define AbstandsmesserTrigger 27
#define AbstandsmesserSensor 26

#define MotorL 22
#define MotorR 23

#define Beeper 4

TaskHandle_t Task1;
TaskHandle_t Task2;

//Variablen Deklarieren
String header;
String Linienfolgen = "Aus";
String Lichtfolgen = "Aus";
String ManuellBetrieb = "Aus";
String MotorSteuerungL = "Aus";
String MotorSteuerungR = "Aus";

int fall = 0;
int abstand;

byte WertSpeed = 180;
byte WertGerade = 90;
byte WertKurve = 13;

bool LiniensensorWertL;
bool LiniensensorWertR;

int SchwellenwertLicht = 3400;
int LichtwiderstandWertL;
int LichtwiderstandWertR;

String boost = "Aus";

//Abstandssensor erstellen
HCSR04 hcsr04(AbstandsmesserTrigger, AbstandsmesserSensor, 20, 4000);

//Netzwerk Daten
const char* ssid = "Roboter Konrad";
const char* passwort = "1235";

WiFiServer server(80);

void setup() {
  Serial.begin(9600);

  //Pin Modes Setzen
  pinMode(BlinkerL, OUTPUT);
  pinMode(BlinkerR, OUTPUT);

  pinMode(FotowiderstandL, INPUT);
  pinMode(FotowiderstandR, INPUT);

  pinMode(LiniensensorL, INPUT);
  pinMode(LiniensensorR, INPUT);

  pinMode(LED_BUILTIN, OUTPUT);

  //Motoren konfigurieren
  ledcAttachPin(MotorL, 1);
  ledcSetup(1, 4000, 8);

  ledcAttachPin(MotorR, 2);
  ledcSetup(2, 4000, 8);

  ledcAttachPin(Beeper, 3);
  ledcSetup(3, 400, 8);

  //Access Point starten
  WiFi.softAP(ssid, passwort);
  IPAddress IP = WiFi.softAPIP();
  Serial.println(IP);
  server.begin();

  xTaskCreatePinnedToCore(
    webserver,   /* Task function. */
    "Server",     /* name of task. */
    10000,       /* Stack size of task */
    NULL,        /* parameter of the task */
    1,           /* priority of the task */
    &Task2,      /* Task handle to keep track of created task */
    0);          /* pin task to core 0 */
  delay(500);

  xTaskCreatePinnedToCore(
    switchTask,   /* Task function. */
    "Switch",     /* name of task. */
    10000,       /* Stack size of task */
    NULL,        /* parameter of the task */
    1,           /* priority of the task */
    &Task1,      /* Task handle to keep track of created task */
    1);          /* pin task to core 0 */
  delay(500);
}
void loop() {

}

void switchTask(void * pvParameters) {
  Serial.print("SwitchTask: ");
  Serial.println(xPortGetCoreID());
  for (;;) {
    switch (fall) {
      case 0:
        digitalWrite(LED_BUILTIN, HIGH);
        ledcWrite(1, 0);
        ledcWrite(2, 0);
        digitalWrite(BlinkerL, LOW);
        digitalWrite(BlinkerR, LOW);
        break;

      case 1:
        digitalWrite(LED_BUILTIN, LOW);
        Linie();
        break;

      case 2:
        digitalWrite(LED_BUILTIN, LOW);
        Licht();
        break;

      case 3:
        digitalWrite(LED_BUILTIN, LOW);
        Manuell();
        break;
    }
    delay(1);
  }
}

void Linie() {
  LiniensensorWertL = digitalRead(LiniensensorL);
  LiniensensorWertR = digitalRead(LiniensensorR);
  if (LiniensensorWertL && LiniensensorWertR) {
    ledcWrite(1, 0);
    ledcWrite(2, 0);
    digitalWrite(BlinkerL, HIGH);
    digitalWrite(BlinkerR, HIGH);
    ledcWrite(3, 255);
  }
  else if (LiniensensorWertL && !LiniensensorWertR) {
    ledcWrite(1, WertKurve);
    ledcWrite(2, WertGerade);
    digitalWrite(BlinkerL, HIGH);
    digitalWrite(BlinkerR, LOW);
    ledcWrite(3, 0);
  }
  else if (!LiniensensorWertL && LiniensensorWertR) {
    ledcWrite(1, WertGerade);
    ledcWrite(2, WertKurve);
    digitalWrite(BlinkerL, LOW);
    digitalWrite(BlinkerR, HIGH);
    ledcWrite(3, 0);
  }
  else {
    if (boost == "An") {
      ledcWrite(1, WertSpeed + 10);
      ledcWrite(2, WertSpeed);
    } else {
      ledcWrite(1, WertGerade + 10);
      ledcWrite(2, WertGerade);
    }
    digitalWrite(BlinkerL, LOW);
    digitalWrite(BlinkerR, LOW);
    ledcWrite(3, 0);
  }
}

void Licht() {
  LichtwiderstandWertL = analogRead(FotowiderstandL);
  LichtwiderstandWertR = analogRead(FotowiderstandR);
  if (LichtwiderstandWertL < SchwellenwertLicht && LichtwiderstandWertR < SchwellenwertLicht) {
    ledcWrite(1, WertGerade + 10);
    ledcWrite(2, WertGerade);
  }
  else if (LichtwiderstandWertL < SchwellenwertLicht && LichtwiderstandWertR > SchwellenwertLicht) {
    ledcWrite(1, WertKurve);
    ledcWrite(2, WertGerade);
  }
  else if (LichtwiderstandWertL > SchwellenwertLicht && LichtwiderstandWertR < SchwellenwertLicht) {
    ledcWrite(1, WertGerade);
    ledcWrite(2, WertKurve);
  }
  else {
    ledcWrite(1, 0);
    ledcWrite(2, 0);
  }
}

void Manuell() {
  if ( MotorSteuerungL == "An" && MotorSteuerungR == "An") {
    ledcWrite(1, WertGerade + 10);
    ledcWrite(2, WertGerade);
  } else if ( MotorSteuerungL == "An" && MotorSteuerungR == "Aus") {
    ledcWrite(1, WertGerade);
    ledcWrite(2, WertKurve);
  } else if ( MotorSteuerungL == "Aus" && MotorSteuerungR == "An") {
    ledcWrite(1, WertKurve);
    ledcWrite(2, WertGerade);
  } else {
    ledcWrite(1, 0);
    ledcWrite(2, 0);
  }
}
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

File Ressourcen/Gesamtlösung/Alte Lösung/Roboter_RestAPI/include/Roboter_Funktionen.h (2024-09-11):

#include "esp32-hal-ledc.h"
#define LOGGING (false)
//---------------------------------------------------------------------------------
////--------------------------------- PIN BELEGUNG --------------------------------
//---------------------------------------------------------------------------------
#define ABSTAND_TRIGGER 27
#define ABSTAND_ECHO 26

#define BEEPER 4

#define LED_links 13
#define LED_rechts 14

#define LICHT_links 33
#define LICHT_rechts 32

#define LINIE_links 18
#define LINIE_rechts 19

#define MOTOR_links 22
#define MOTOR_rechts 23


typedef enum fahrtrichtung {
  stopp,
  vorwaerts, 
  links,
  rechts,
}fahrtrichtung_t;


bool FOLGE_LINIE  = false;
bool FOLGE_LICHT  = false;
bool ABSTAND_MESSEN = false;

byte linienfarbe;                                                             // High fuer Schwarz-auf-weiss / Low fuer weiss-auf-schwarz
// bool start = false;

//---------------------------------------------------------------------------------
////---------------------------------- VARIABLEN ----------------------------------
//---------------------------------------------------------------------------------

// Konstanten fuer Abstandssensor
const int maxRange = 300;                                                           // maximal messbarer Abstand
const int minRange = 2;                                                             // minimal messbarer Abstand
const int abstand_grenze = 15;                                                      // Abstand bei dem gestopppt werden soll

// Variablen fuer Abstandssensor
long abstand;                                                                       // Variable fuer gemessenen Abstands
long dauer;                                                                         // Variable fuer Zeitdauer der Messung
int abstand_loop = 0;                                                               // Counter fuer Schleifendurchlaeufe, Mittelwert aus 10 Messungen wird verwendet
int abstand_summe = 0;                                                              // Variable fuer insgesamt in 10 Messungen ermittelten Wert


// Konstanten fuer Lichtsensoren
const int messtoleranz = 50;                                                       // Messwert-Abweichung zw. Sensoren ca. 150-250
const int prozent_einstrahlung = 110;                                               // bei zusaetzlicher Einstrahlung (z.B. Taschenlampe) gemessener Wert ca. 25% hoeher als normal
//const int prozent_einstrahlung = 125;                                             // bei zusaetzlicher Einstrahlung gemessener Wert ca. 25% hoeher als normal
//const int prozent_einstrahlung = 125;                                             // bei zusaetzlicher Einstrahlung gemessener Wert ca. 25% hoeher als normal

// Variablen fuer Lichtsensoren
int lichtWert_durchschnitt;                                                         // durchschnittlich gemessener Helligkeitswert fuer Vergleich mit Umgebungshelligkeit
int lichtWert_links_summe = 0;                                                      // insgesamt bei bisherigen Schleifendurchläufen gemessener Wert, links
int lichtWert_rechts_summe = 0;                                                     // insgesamt bei bisherigen Schleifendurchläufen gemessener Wert, rechts
int loop_count = 0;                                                                 // Counter fuer Schleifendurchlaeufe, Mittelwert aus 10 Messungen wird verwendet
int lichtWert_links = 1;                                                            // aktuell gemessener Helligkeits-Wert rechts, auf 1 gesetzt um durch 0 teilen zu vermeiden
int lichtWert_rechts = 1;                                                           // aktuell gemessener Helligkeits-Wert links, auf 1 gesetzt um durch 0 teilen zu vermeiden
int lichtWert_umgebung = 1;                                                         // Umgebungshelligkeit, auf 1 gesetzt um durch 0 teilen zu vermeiden


// Konstanten fuer Motor-PWM
const int freq = 15000;                                                             // PWM Frequenz
const int motorChannel_links = 0;                                                   // PWM Kanal fuer linken Motor
const int motorChannel_rechts = 2;                                                  // PWM Kanal fuer rechten Motor
const int resolution = 9;                                                           // PWM-Aufloesung
const int max_velocity = (int) (pow(2, resolution) - 1);                      // max. Wert fuer PWM ist 2^(aufloesung) -1

int velocity_driveoff = 0.6 * max_velocity;
int velocity_drive = 0.45 * max_velocity;
int velocity_turn_inside = 0.34 * max_velocity;
int velocity_turn_outside = 0.75 * max_velocity;    //0,65
int velocity_stopp = 0;


// Konstanten zum Blinken der LEDs
const long BLINK_INTERVAL = 500;                                                    // Zeitinterval (Millisekunden) in dem LEDs blinken sollen

// Variablen zum Blinken der LEDs
int ledState = LOW;                                                                 // Status der LED zum Blinken (wechselt zw. high und low)
unsigned long previousMillis_led = 0;                                               // letzter Zeitpunkt zu dem LED gesetzt wurde


// Konstanten fuer Beeper-PWM
const int beeperFreq = 1000;                                                        // Ton Frequenz für Ton C
const int beeperChannel = 4;                                                        // PWM Kanal fuer Beeper
const int beeperResolution = 4;                                                     // PWM-Aufloesung
const int beeper_off = 0;
const int beeper_on = 0.5 * (pow(2, beeperResolution) - 1);

// Konstanten zum Hupen
const long BEEPER_INTERVAL = 10;                                                  // Zeitinterval (Millisekunden) in dem Beeper ein- und ausgeschaltet werden soll

// Variablen zum Hupen
int pinState = LOW;                                                                 // Status des Pins zum Hupen (wechselt zw. high und low)
unsigned long previousMillis_beeper = 0;                                            // letzter Zeitpunkt zu dem Beeper gesetzt wurde


// Variablen fuer Programmablauf
fahrtrichtung_t fahrtrichtung = stopp;
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

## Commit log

2022-06-10 Readme's als Zusammenfassung des Inhaltes ergänzt
2022-06-24 Materialliste Einführungsaufgaben erstellt
2022-10-10 Dateien für 3D-Druck Stützkugel hinzugefügt
    [Halbkugel 1cm Durchmesser - Praktikanten Projekt v1.3mf, Halbkugel 1cm Durchmesser - Praktikanten Projekt v1.f3d, Halbkugel 1cm Durchmesser - Praktikanten Proj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]
2023-02-10 Update Halbkugel 1cm Durchmesser - Praktikanten Projekt v1.3mf
    [Halbkugel 1cm Durchmesser - Praktikanten Projekt v1.3mf]
2023-03-09 update material list for part 2 and part 3
2023-06-13 add missing resistors
2023-09-12 move files
    [Halbkugel 1cm Durchmesser - Praktikanten Projekt v1.3mf, Halbkugel 1cm Durchmesser - Praktikanten Projekt v1.f3d, Halbkugel 1cm Durchmesser - Praktikanten Proj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]
2023-09-12 add chassi files
    [Chassis_V1_Drucken.prt, Chassis_V1_Drucken.stl, Chassis_V2_Drucken.prt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]
2023-10-09 Gerberfile und Allgemeine Beschreibung hinzugefügt
2023-10-10 doppelte esp32 Lösung entfernt
2023-10-12 Felge V1 hinzugefügt
    [AW1082-02-62-50-000_Felge_V1.prt, AW1082-02-62-50-000_Felge_V1.stl]
2024-10-16 added materiallist and pagesconfig
2024-10-23 Organization changes and File Additions
    [AW1082-02-62-50-000_Felge_V1.prt, AW1082-02-62-50-000_Felge_V1.stl, Chassis_V1_Drucken.prt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]
2024-11-06 Überarbeitung des Einführungsdokuments
2024-11-13 Adjusted Material List
2024-11-13 Added Build Option and Grammer changes
    Another Method to keep the Front off the Ground and the File was missing a dot.
2024-11-13 Changes to the Material List
    Removed additional Text that was irritating in hindsight
2024-11-13 Added Resistor Pictures
    Will be used for Reference in Tasks
2024-11-20 Notizen zu Widerständen eingefügt
    Anmerkung, dass man die Widerständ im Voraus messen soll.
2024-11-20 Link zu der Einführungs PDF hinzugefügt.
2024-11-20 Buchsenleiste für Ultraschallsensor
    Buchsenleiste für Ultraschallsensor mit aufgelistet, entsprechende Änderungen in Material und Lötanleitung
2024-11-20 Gesamtlösung-Struktur angepasst und Lösungscode hinzugefügt
2024-11-20 Fertigstellung vom der Select auswahl für Linienfarbe
2025-01-22 Reworked Webserver and Solution
    [Loesung_Webserver.ino]
2025-01-22 Update der Lösung Zip
2025-10-14 switched from "Sie" to "Du"
2025-10-15 The Webserver-UI now follows the corporate-design-guidelines of WAGO
    - Controls are "WAGO Green" or "WAGO Anthrazit"
    - Website header and title are now "WAGO Linienroboter" instead of "ESP32 control"
2025-10-15 Update Webserver.cpp
    Switched to WAGO-Color-Theme
